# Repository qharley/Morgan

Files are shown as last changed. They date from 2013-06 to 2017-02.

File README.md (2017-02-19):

RepRAP Morgan Classic
======

RepRAP Morgan scad source repository
GPLv2 2013

This is the source of the original Morgan design.
See the RepRapMorgan organisation for new versions.
https://github.com/RepRapMorgan

Lilian is the latest open sourced version at the time of writing.

Please find more information on this project at its web home http://www.morgan3dp.com

Please feel free to use it to make your own Morgan.

Quentin Harley

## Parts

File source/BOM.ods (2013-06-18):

Component | Quantity
01-pvc_pipe_support_a | 4
02-pvc_pipe_support_b | 4
03-z_mount_bottom_8mm | 1
04-z_mount_top_8mm | 1
05-motormount_short | 1
06-motormount_tall | 1
07-drivewheel_rod | 1
08-drivewheel_tube | 1
09-22mm_6805_bearing_adaptor | 1
10-bed_arm_left_8mm | 1
11-bed_arm_right_8mm | 1
12-bed_z_mount_bracket | 1
13-bed_rear_mountclips | 2
15mm pipe holders – To be done | 2
15-hall_endstop_holder | 3
16-leadscrew_shaft_motor_mount | 1
17-Morgan_arm_PSI_a | 1
18-Morgan_arm_PSI_b | 1
19-Morgan_arm_Theta_a | 1
20-Morgan_arm_Theta_b | 1
21-Morgan_toolhead | 1
22-Leadscrew-nut_Alpen8mmSDS | 1
23-extruder_bowden_adaptor | 1
Cap_2 | 2
Eckstruder_Big_Gear_Herringbone | 1
Eckstruder_Block_for_Prusa | 1
Eckstruder_Idler_Block_for_Prusa | 1
Eckstruder_Small_Gear_Herrinbone | 1
thumb_knob_M4_extruder | 1
TighteningCone_2 | 2
M8 nut | 12
M8 washer | 6
M8 spring washer | 10
M8 washer 28mm | 6
M4 nut | 9
M4 bolt 40mm | 8
M4 bolt 80mm | 1
M8 Nylock Nut | 6
M8 Bolt 40mm | 3
M8 Bolt 100mm | 1
M8 Bolt 60mm | 1
PVC pipe 32mm OD 459mm | 2
PVC pipe 32mm OD 452mm | 2
2mm self tapping coach screws, 40mm | 2
15mm brass pipe 440mm | 1
15mm brass pipe 200mm | 2
22mm brass pipe 460mm | 1
8mm threaded rod 650mm | 1
8mm smooth rod | 2
608z | 5
F608z | 4
hard spring (idler compression) 7mm | 1
8mm soft spring (lead screw anti backlash | 1
cabinet coach screws, 5mm | 10
LM8uu bearing or alternative | 4
lead screw 330mm | 1
M3 nut | 3
M3 grub screw 6mm (or suitable replacement bolt | 3
hall effect endstop sensors | 3
Electronics | 1
Pololu low current 1/16th | 2
Pololu high current 1/32th | 2
Step motor 200step (1.8deg) | 2
Step motor 400step (0.9deg (if possible – otherwise increase other motors) | 2
Power supply AXT 400W minimum | 1
PTFE tube 6mm 600mm | 1
Additional PTFE tube 4mm 600mm (Only if 1.75mm J-head) | 1
Morgan lasercut platforms | 1
Universal build plate | 1
Mk2a heatbed | 1
aluminium build surface | 1
Ethernet cable, multistrand flexible, m | 5
High current cable, heatbed m | 1

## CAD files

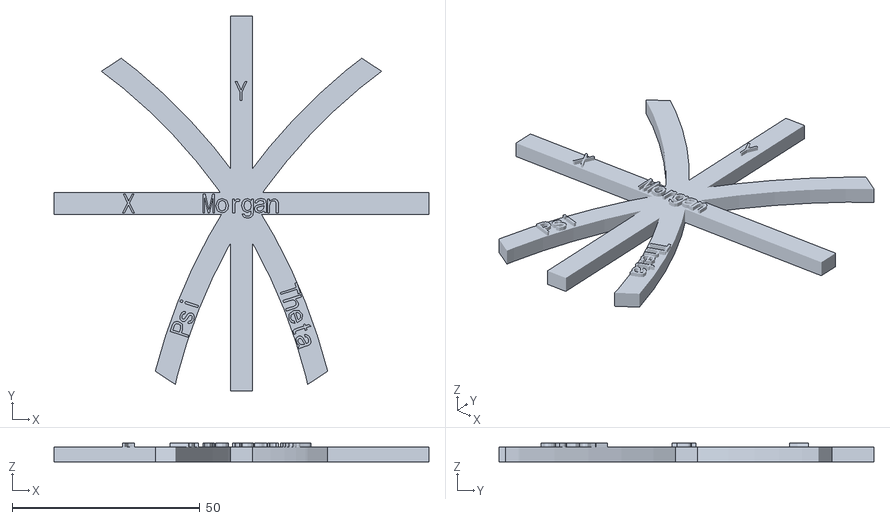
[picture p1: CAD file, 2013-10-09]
calibration/SCARA-CAL.stl
100.0 x 100.0 x 5.00

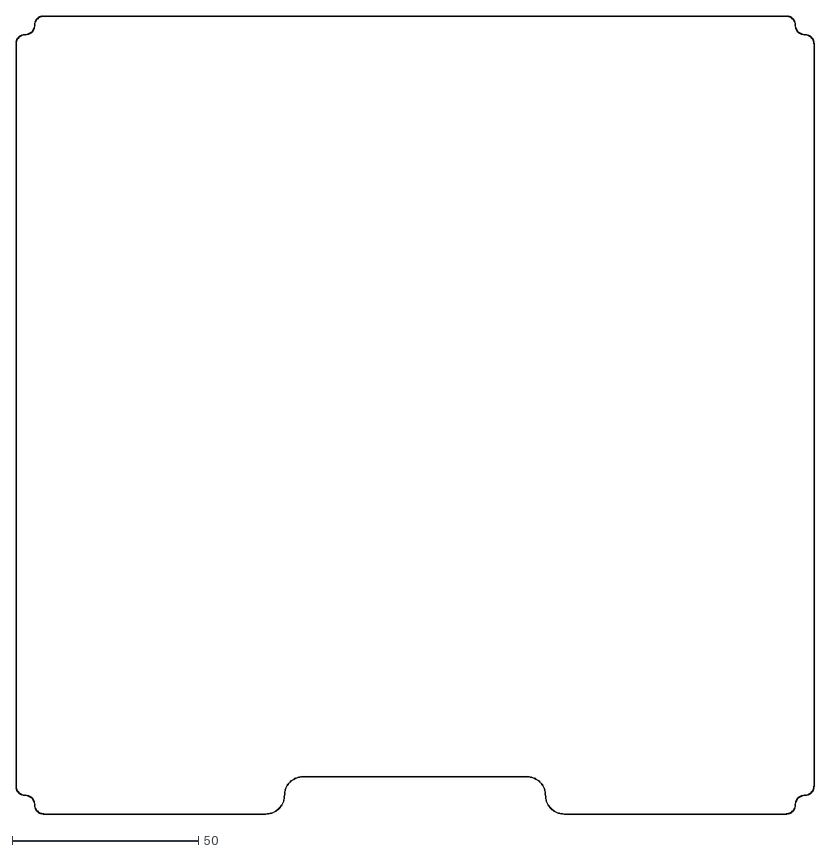
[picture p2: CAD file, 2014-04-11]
dxf/BuildPlate4_by_gineer.dxf
214.0 x 214.0

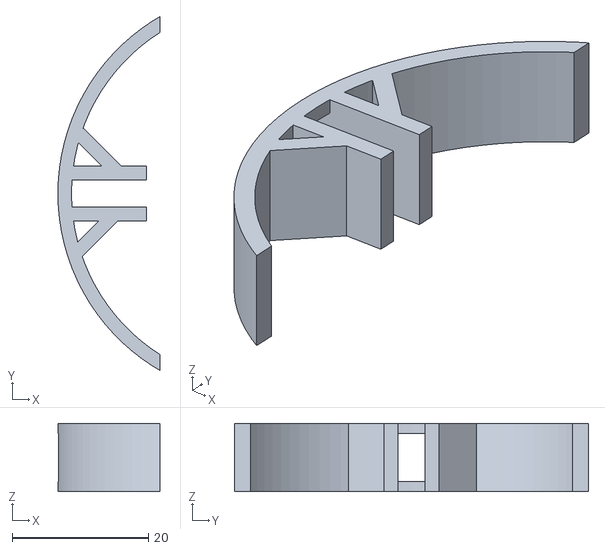
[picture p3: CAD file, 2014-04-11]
source/belt clip.stl
15.0 x 51.9 x 10.0

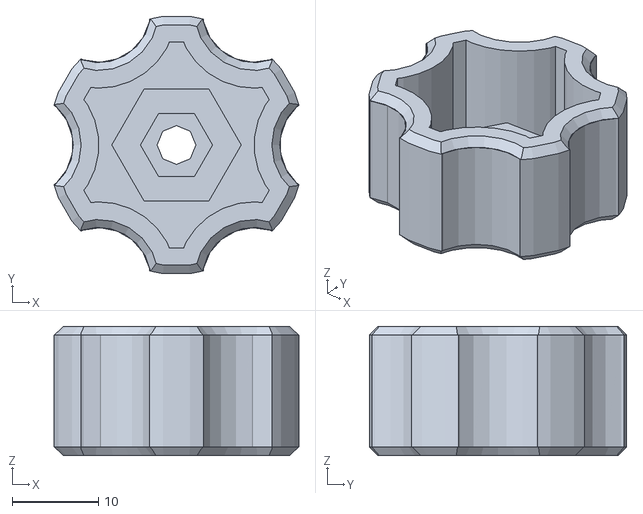
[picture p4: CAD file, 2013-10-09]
stl/Eckstruder-3mm/thumb_knob_M4_extruder.stl
28.4 x 29.8 x 15.0

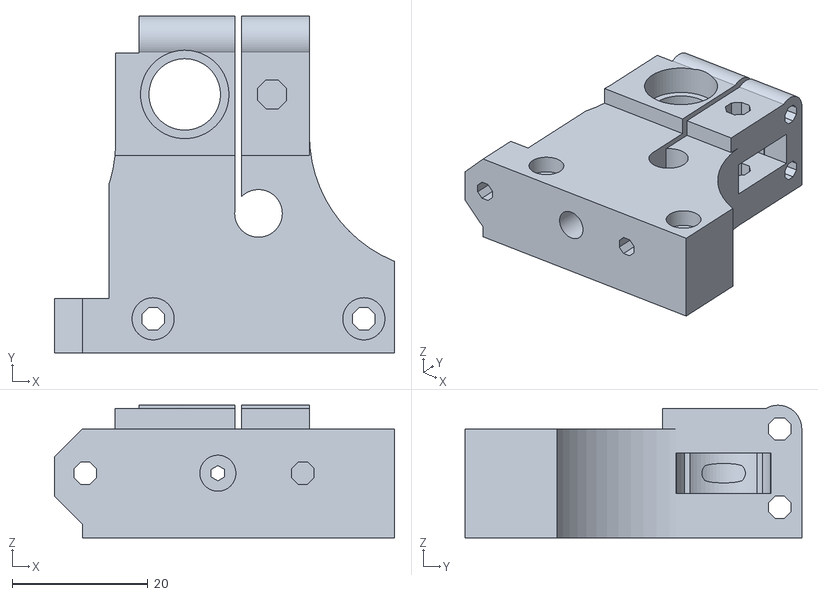
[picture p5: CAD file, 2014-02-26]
stl/Morgan-extruder-1.75mm/extruder-drive-1off.stl
50.0 x 49.5 x 19.5

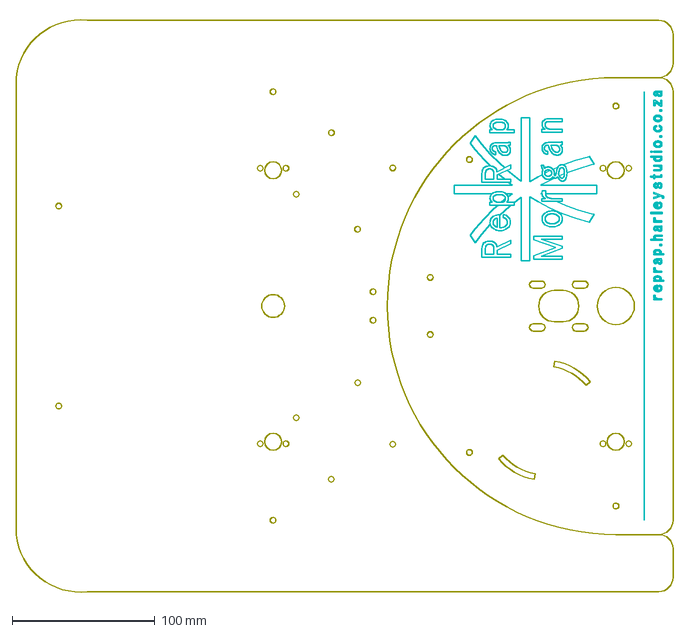
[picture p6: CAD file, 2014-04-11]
dxf/platform_cut_engrave_mk2.dxf
460.0 x 404.1 mm

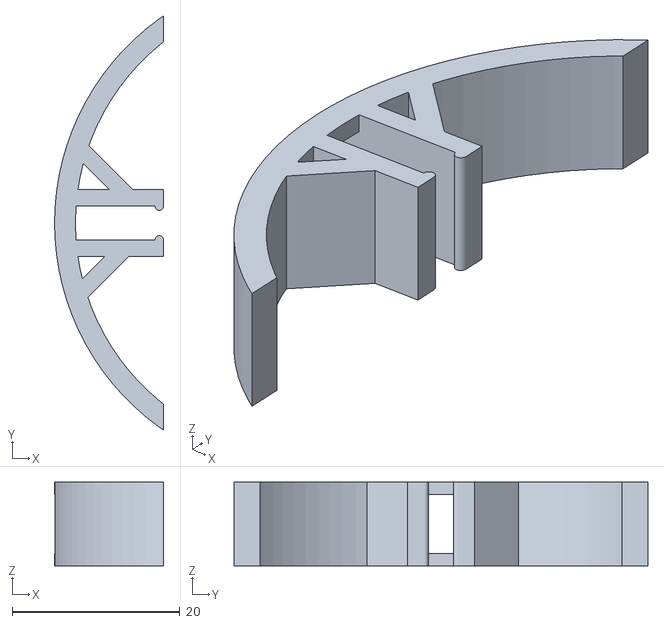
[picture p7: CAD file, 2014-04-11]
stl/28-Morgan_belt_clip.stl
13.0 x 49.4 x 10.0

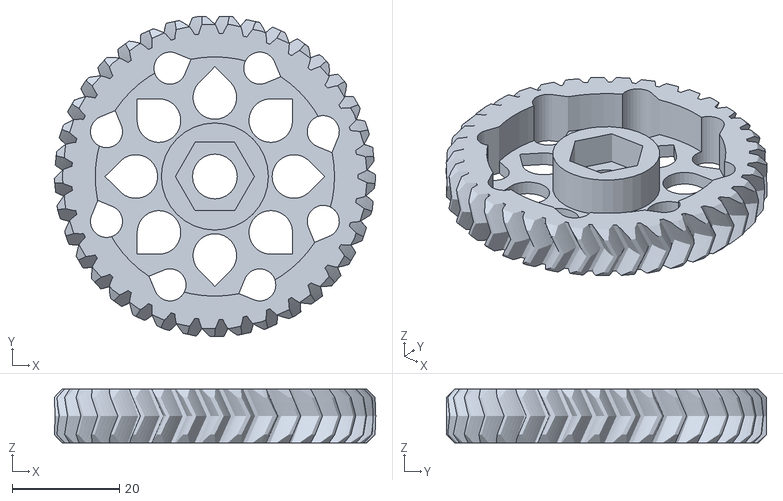
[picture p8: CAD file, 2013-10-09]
stl/Eckstruder-3mm/Eckstruder_Big_Gear_Herringbone.stl
60.1 x 59.8 x 10.0

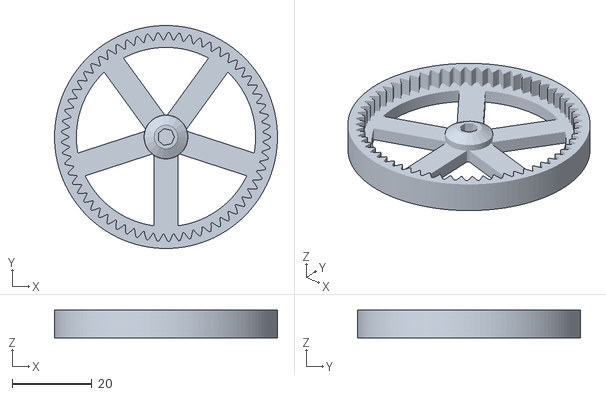
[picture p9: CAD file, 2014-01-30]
stl/Morgan-extruder-1.75mm/large-gear-1off.stl
56.0 x 56.0 x 7.00

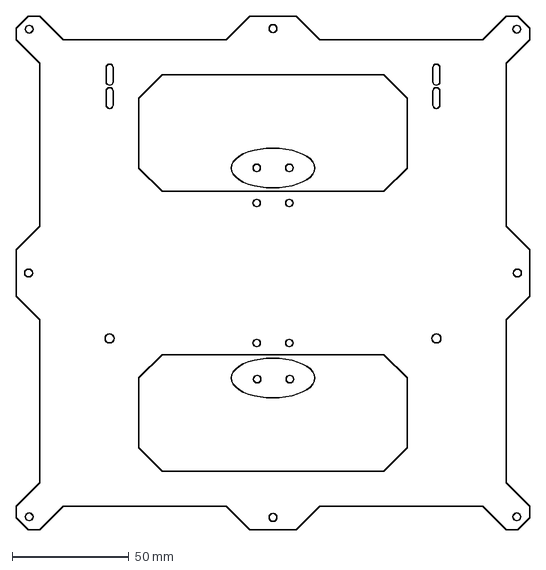
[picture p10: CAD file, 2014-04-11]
dxf/Morgan_bed_base.dxf
220.0 x 220.0 mm

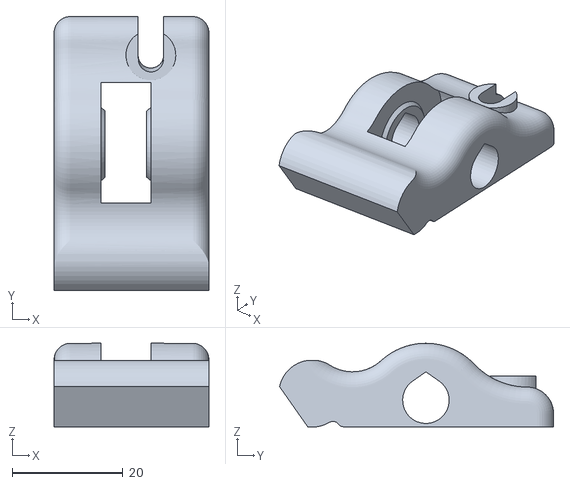
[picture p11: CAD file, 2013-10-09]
stl/Eckstruder-3mm/Eckstruder_Idler_Block_for_Prusa.stl
28.0 x 49.5 x 15.1

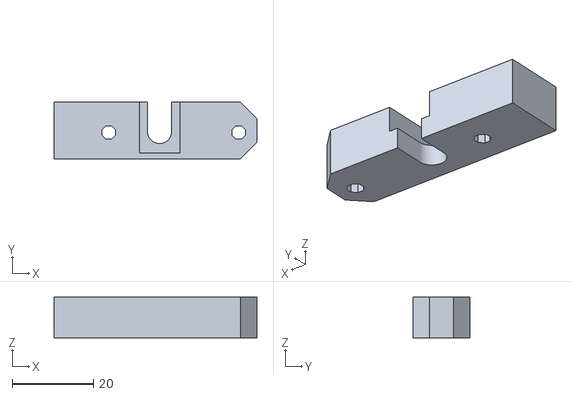
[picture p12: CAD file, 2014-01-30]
stl/Morgan-extruder-1.75mm/6mm-ptfe-clamp-1off.stl
50.0 x 14.0 x 10.0

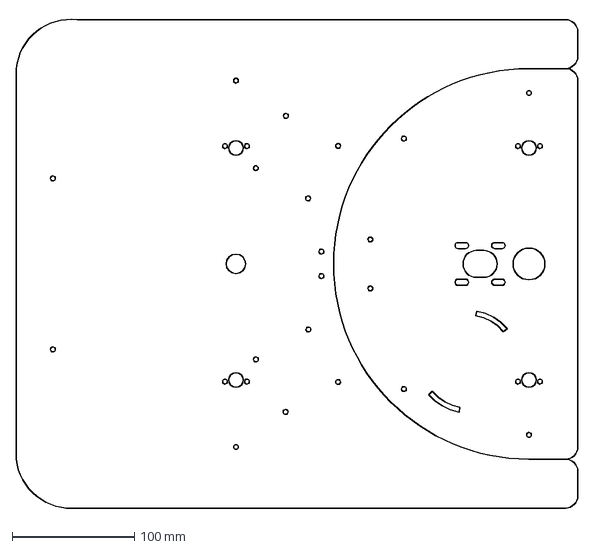
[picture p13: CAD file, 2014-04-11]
dxf/platform_cut_mk2.dxf
460.0 x 404.1 mm

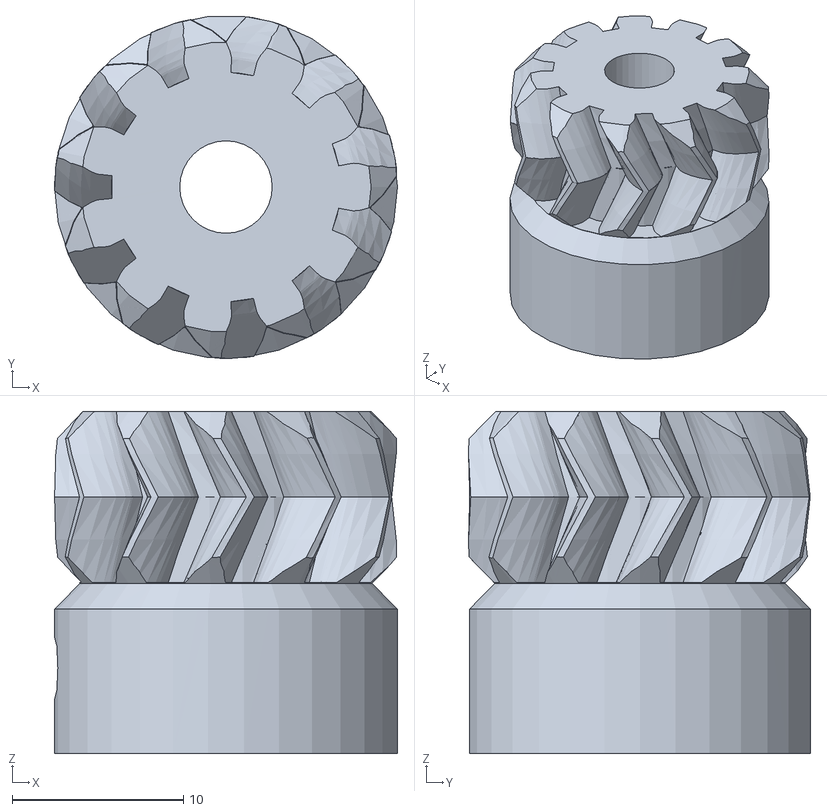
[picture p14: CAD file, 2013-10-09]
stl/Eckstruder-3mm/Eckstruder_Small_Gear_Herringbone.stl
20.0 x 20.0 x 20.0

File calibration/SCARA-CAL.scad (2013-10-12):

// Morgan SCARA Calibration phantom

use <Writescad/Write.scad>;   // get it here... http://www.thingiverse.com/thing:16193
use <MCAD/polyholes.scad>;
Linkage = 150;	//	Arm segment nominal length (as programmed in Firmware)

xoffset = -35;	// Scara tower offset (as programmed in firmware)
yoffset = -65;

K1 = 0;
K2 = 0;

theta = 0;
psi = 0;

xpos = 125.27;
ypos = 82.5;

cal_angle = 33.367;

arm_width = 6;
arm_height = 4;



//projection(cut = false)
	SCARAcal();

$fn=100;

module SCARAcal(){


	intersection(){
		translate([-xpos,ypos+yoffset,-1])
			difference(){
				cylinder(r=Linkage + 3, h=arm_height+2);
				cylinder(r=Linkage - 3, h=arm_height+2);
	
			}
		translate([-xpos,ypos+yoffset,0])
		rotate([0,0,cal_angle])
			translate([100,-50,0])
				cube([100,100,arm_height]);
	}

	intersection(){
		translate([xpos,ypos+yoffset,-1])
			difference(){
				cylinder(r=Linkage + arm_width/2, h=arm_height+2);
				cylinder(r=Linkage - arm_width/2, h=arm_height+2);
	
			}
		translate([xpos,ypos+yoffset,0])
		rotate([0,0,180-cal_angle])
			translate([100,-50,0])
				cube([100,100,arm_height]);
	}

	translate([0,100,arm_height/2]){
		cube([100,arm_width,arm_height],center=true);
		cube([arm_width,100,arm_height],center=true);
	}

	translate([16,70,arm_height])
		#write("Theta",t=2,h=6,rotate=72,center=true);

	translate([-16,70,arm_height])
		#write("Psi",t=2,h=6,rotate=-72,center=true);

	translate([0,130,arm_height])
		#write("Y",t=2,h=7,rotate=0,center=true);

	translate([-30,100,arm_height])
		#write("X",t=2,h=7,rotate=90,center=true);

	translate([0,101,arm_height])
		#write("Morgan",t=2,h=6,rotate=0,center=true);
	
}

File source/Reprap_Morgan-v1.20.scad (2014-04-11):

//---------------------------------------------------------------------------------------------------
// RepRap "Morgan", main ver 1.20 - Single extruder version
// Copyright 2012, 2013. Author: Quentin Harley (qharley)
// This original design is licensed under GPLv2.
//
// These are the main SCARA arm components

include <MCAD/teardrop.scad>
include <MCAD/polyholes.scad>
include <MCAD/nuts_and_bolts.scad>

LMxUU = 8;				// Choose linear bearing: 8 or 12mm
rodspacing = 175;		// Distance between rods:	175 standard, 190 wide
PVC_pipe_OD = 32;		// Default 32mm
PVC_pipe_ID = 27.5;	// measure pipe ID to adjust
Drive_pipe_OD = 22.5;	// Drive pipe outter diameter: 22mm default
THREADLESS = false;	// True for use of threadless ball screw in z-bracket
SUPPORTED_ROD = true;	// Rods held by Z-mounts - False for platform mounted (lasercut)
Leadnut_thread = false;// Apply the thread of the leadscrew nut to the Z coupler

ENVELOPE_CHECK = false;

MakeMorgan(05);		// Select Part number to make	

//MorganEndstopZ();
//***********************************************************
//**                                                			**
//**    Select the number of the module to make				**
//**																		**
//**	01:	 PVC pipe support A (Ported, 458.5mm pipe)			**
//**	02:	 PVC pipe support B (non Ported, 451.5mm pipe)		**
//**	03: Z-mount Bottom												**
//**	04: Z-mount Top													**
//**	05: Motormount Short											**
//**	06: Motormount Tall											**
//**	07: Rod mounted Drivewheel									**
//**	08: Tube mounted Drivewheel									**
//**	09: 22mm Tube 6805 bearing adaptor							**
//**	10: Bed arm Left												**
//**	11: Bed arm Right												**
//** 	12:	 Bed Z-bracket and lead screw holder					**
//**	13: Bed rear mounting clips									**
//**	14: Bed front mounting clips									**
//**	15: hall-endstop holders										**
//**	16: Z-Lead screw motor shaft coupler						**
//**	17: Arm PSI A (inner supporting arm)						**
//**	18: Arm PSI B (outer supporting arm)						**
//**	19: Arm Theta A (inner steering arm)						**
//**	20: Arm Theta B (outter steering arm)						**
//**	21: Morgan Tool head (make from ABS/Nylon/etc)		**
//**	22: Lead screw nut (Alpen 8mm SDS)	
//**	23: extruder Bowden adaptor
//**  24: Belt anchor clip
//
//**  25: Morgan Line wheel (Rod mount)
//**  26: Morgan Line Wheel (Tube mount)				
//**
//**  TO DO!  Build Plates...
//**		Select number of build plate
//**	50: Arms Plate 		(PLA)
//**	51: Bed Plate 1		(PLA)
//**	52: Bed Plate 2		(PLA)
//**	55: Wheel PlateA	(PLA)
//**	56: Wheel PlateB	(PLA)
//**	60: Diverse Plate	(ABS)



module MakeMorgan(partnumber)
{
	if (partnumber == 1 ){
		MorganPVCsupport_ANG(PVC_pipe_ID,130,130,420, pipe = false, port=true);	// 458.47
	}
	if (partnumber == 2 ){
		MorganPVCsupport_ANG(PVC_pipe_ID,70,150,420, pipe = false);					// 451.44
	}
	
  rotate([0,0,45]){ 					// parts rotated through 45deg to ease fitting to RepRap heatbed


//MorganPillarMount();
//MorganShaftMount();
	if (partnumber == 3 ){
		if (SUPPORTED_ROD){
			MorganZmountBot(rodspacing, LMxUU);
		}
		else {
			MorganShaftMount();
		}		
	}
	if (partnumber == 4 ){
		if (SUPPORTED_ROD){
			MorganZmountTop(rodspacing, LMxUU);
		}
		else {
			MorganPillarMount();
		}	
		
	}

  }

	if (partnumber == 5 ){
		MorganMotorMount4(Height = 50);
	}
	if (partnumber == 6 ){
		mirror()
			MorganMotorMount4(Height = 70);
	}
	if (partnumber == 7 ){
		MorganBeltWheel();			// Rod mounted belt drive wheel
	}
	if (partnumber == 25 ){
		MorganLineWheel();			// Rod mounted line drive wheel
	}
	if (partnumber == 8 ){
		MorganBeltWheel2();			// Tube mounted belt drive wheel
	}
	if (partnumber == 26 ){
		MorganLineWheel2();			// Tube mounted line drive wheel
	}
	if (partnumber == 9 ){
		MorganPillar();				// 6805 bearing tube mount
	}
	
  rotate([0,0,45]){

	if (partnumber == 10 ){
		if(LMxUU == 12)
			MorganBedarmLeft(21.5);
		else
			MorganBedarmLeft(15.5);
	}
	if (partnumber == 11 ){
		if(LMxUU == 12)
			MorganBedarmRight(21.5);
		else
			MorganBedarmRight(15.5);
	}
	if (partnumber == 12 ){
		//Bed_stabil_bracket(21.5);
		if(LMxUU == 12)
			Bed_stabil_bracket(21.5);
		else
			Bed_stabil_bracket(15.5);
	}

  }

	if (partnumber == 13 ){
		BedMountRear();
	}
	if (partnumber == 14 ){
		BedMountFront();
	}
	
	if (partnumber == 15 ){
		MorganEndstop();
	}

	if (partnumber == 16 ){
		rotate([0,0,45])
			MorganZCoupler();
	}
	if (partnumber == 17 ){
		Primary_Arm();
	}
	if (partnumber == 18 ){
		Secondary_Arm();
	}
	if (partnumber == 19 ){
		Sup_Arm1();
	}	
	if (partnumber == 20 ){
		Sup_Arm2();
	}
	if (partnumber == 21 ){
		//Secondary_Arm_hotend_holder_mk2(Hotend_D = 16.5, Hotend_H = 12);
		Secondary_Arm_hotend_holder_mk2(Hotend_D = 16.5, Hotend_H = 12+25,mountpiece = true);
	}
	if (partnumber == 22 ){
		leadscrew_nut();
	}
	if (partnumber == 23 ){
		Extruder_Bowden_adaptor(support = false);
	}
	if (partnumber == 24 ){
		belt_clip();;
	}

	
//**************** Plates  ***************************

	if (partnumber == 50 ){
		translate([0,0,0])
			Primary_Arm();
		translate([0,35,0])
			Secondary_Arm();
		translate([0,-35,0])
			Sup_Arm1();
		translate([0,73,0])
			Sup_Arm2();
		
	}

	if (partnumber == 51 ){
		rotate([0,0,45]){
			translate([-13,0,0])
				if(LMxUU == 12)
					MorganBedarmLeft(21.5);
				else
					MorganBedarmLeft(15.5);

			translate([13,0,0])
				if(LMxUU == 12)
					MorganBedarmRight(21.5);
				else
					MorganBedarmRight(15.5);
		}

		translate([0,60,0])
			BedMountRear();
		translate([-40,150,0])
			rotate([0,0,180])
				BedMountRear();

		translate([-120,50,15/2])
			BedMountFront();
		translate([-120,20,15/2])
			BedMountFront();

	}


	if (partnumber == 60 ){
		translate([0,0,0])
			rotate([0,0,0])
				Secondary_Arm_hotend_holder(Hotend_D = 16.5, Hotend_H = 12);

		translate([70,-10,0])
			rotate([0,0,180])
				MorganPVCsupport_ANG(26.5,130,130,420, pipe = false, port=true);	// 458.47
	
		translate([-40,0,0])
			rotate([0,0,180])
				MorganPVCsupport_ANG(26.5,130,130,420, pipe = false, port=true);	// 458.47

		translate([-50,40,0])
			rotate([0,0,0])
				MorganPVCsupport_ANG(26.5,70,150,420, pipe = false);					// 451.44
		
		translate([-50,-70,0])
			rotate([0,0,0])
				MorganPVCsupport_ANG(26.5,70,150,420, pipe = false);					// 451.44

		translate([-70,-40,0])
			rotate([0,0,0])
				Extruder_Bowden_adaptor(support = false);

		translate([40,-35,0])
			rotate([0,0,0])
				import("../stl/cap_2.stl");

		translate([-40,-35,0])
			rotate([0,0,0])
				import("../stl/cap_2.stl");

		translate([-30,50,0])
			rotate([0,0,0])
				import("../stl/Eckstruder_Big_Gear_Herringbone.stl");

		translate([-16,-35,20])
			rotate([0,0,0])
				import("../stl/Eckstruder_Small_Gear_Herringbone.stl");

		translate([-50,-25,0])
			rotate([0,0,-90])
				import("../stl/Eckstruder_Idler_Block_for_Prusa.stl");

		translate([50,-65,0])
			rotate([0,0,0])
				import("../stl/thumb_knob_M4_extruder.stl");

		translate([10,110,0])
			rotate([0,0,-90])
				import("../stl/Eckstruder_Block_for_Prusa.stl");

	}

}





// **********************************************************
// **  Here be dragons...

//** print envelope check - only in F5 review
if(ENVELOPE_CHECK){
	translate([0,0,50])
		%cube([200,200,100], center=true);
}

module Matrix_test()
{
	for(x=[0:9])
	{
		for (y=[0:9])
		{
			translate([20*x,20*y,1.5])
				difference(){
					cube([20,20,3], center=true);
					cube([19,19,3],center=true);
				}
		}
	}	
}



PipeFactor = 40/39.2;			// Multiplication factor for inner diameter 

//MorganFrame();

pipeselect = false; // Show pipes in frame... default false


// ************** Building Blocks *************
// MorganPillarMount();
//	MorganShaftMount();
// MorganBedarm_mount();
//Bed_stabil_clasp();

// *****************8***********
//MorganMotorMount(50);
//MorganMotorMount(75);
//MorganFlatMotorMount();

module Dual_toohead()
{
	MakeMorgan(21);		// Select Part number to make	

	translate([150,0,0])
		rotate([0,0,12])
			translate([-150,0,0])
				rotate([0,0,90-(12/2)])
					Secondary_Arm_hotend_holder_2(Hotend_D = 16.5, Hotend_H = 12);
	translate([0,0,27])
		rotate([0,0,50])
			#MakeMorgan(20);
	translate([0,0,2])
		#MakeMorgan(18);
}

module leadscrew_profile()
{
	projection(cut=false){
		//polyhole(5,5);
		cylinder(r=3, h=5, $fn=24);
		cube([7.5, 3,1], center=true);
		rotate([0,0,-45])
			cube([6.5,3,1],center = true);
	}
}

module leadscrew_nut(){
	difference(){
		union(){
			cylinder(r=14.8/2,h=14, $fn=6);

		}
		linear_extrude(height = 120/4, center = true, twist = -360)
			scale(1.1)
				leadscrew_profile();
	}

}

module belt_clip($fn = 100)		// Adapted from code by WJ Harley
{
	difference()	{
		translate([0,0,0])	
			cylinder(10,30,30,0);
		union()
		{	
			translate([-17,-30,-1])
				cube([50,65,12]);
			translate([0,0,-0.2])	
				cylinder(12,r=27.5);
			translate([-35,-2,1.5])
				cube([30,4,7]);
		}
	}
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

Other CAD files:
stl/Morgan-extruder-1.75mm/spacer-1off.stl
dxf/OpenHW_Universal-XPlate.dxf
stl/05-motormount_short_mk5.stl
stl/Eckstruder-3mm/Eckstruder_Block_for_Prusa.stl
source/Reprap_Morgan-v1.00.scad
source/Reprap_Morgan-v1.10.scad
dxf/Morgan_platform_cutting.dxf
stl/01-pvc_pipe_support_a.stl
stl/02-pvc_pipe_support_b.stl
stl/03-z_mount_bottom_12mm.stl
stl/03-z_mount_bottom_8mm.stl
stl/03-z_mount_bottom_noarm.stl
stl/04-z_mount_top_12mm.stl
stl/04-z_mount_top_8mm.stl
stl/04-z_mount_top_nosup.stl
stl/05-motormount_short.stl
stl/06-motormount_tall.stl
stl/06-motormount_tall_mk5.stl
stl/07-drivewheel_rod.stl
stl/08-drivewheel_tube.stl
stl/09-22mm_6805_bearing_adaptor.stl
stl/10-bed_arm_left_12mm.stl
stl/10-bed_arm_left_8mm.stl
stl/11-bed_arm_right_12mm.stl
stl/11-bed_arm_right_8mm.stl
stl/12-bed_z_mount_bracket_12mm.stl
stl/12-bed_z_mount_bracket_8mm.stl
stl/13-bed_rear_mountclips.stl
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

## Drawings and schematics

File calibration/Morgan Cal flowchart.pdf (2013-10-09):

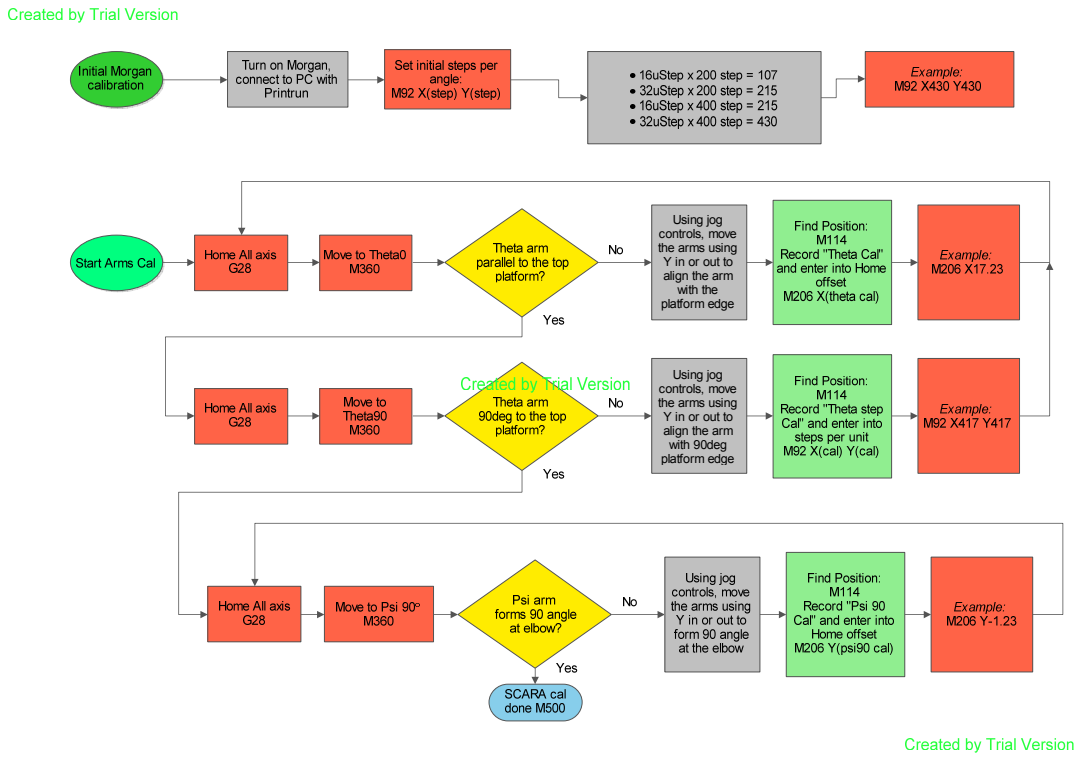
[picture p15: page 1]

Using jog
controls, move
the arms using
Y in or out to
align the arm
with the
platform edge

with 90deg

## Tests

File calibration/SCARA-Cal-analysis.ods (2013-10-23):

Dimension | Measurement |  | Target | Current Step/deg | Scaling Factor | New Step M92 | New factor M365 | after scaling
Theta | 100 | 90.8896776828 | 100.000 | 212.94 |  | 234.28 | 1.1 | 99.979
Psi | 100 | 90.8896776828 | 100.000 | 216.98 |  | 238.73 | 1.1 | 99.979
X | 110 |  | 100.000 |  | 1.023 |  | 0.93 | 100.000
Y | 110 |  | 100.000 |  | 0.998 |  | 0.907 | 99.970
Z

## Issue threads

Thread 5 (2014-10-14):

Straight line drawing

MYasirSheikh, 2014-10-14:
As you know, it's a chunk of code from prepare_move function

Is this part of the code for straight line drawing (since the arm has a tendency of radial movement because of SCARA). If YES, can someone explain me the logic.. I badly need it for some development. help me pleaseeee..

float seconds = 6000 * cartesian_mm / feedrate / feedmultiply;
  int steps = max(1, int(DELTA_SEGMENTS_PER_SECOND * seconds));
  for (int s = 1; s <= steps; s++) {
    float fraction = float(s) / float(steps);
    for(int8_t i=0; i < NUM_AXIS; i++) {
      destination[i] = current_position[i] + difference[i] * fraction;
    }
    calculate_delta(destination);
    plan_buffer_line(delta[X_AXIS], delta[Y_AXIS], delta[Z_AXIS],
                     destination[E_AXIS], feedrate*feedmultiply/60/100.0,
                     active_extruder);
  }

  for(int8_t i=0; i < NUM_AXIS; i++) {
    current_position[i] = destination[i];
  }
}

qharley, 2015-01-02:
It has been quite a while since I did any work on marlin... Mostly my fault since I did not know how to keep the software updated and how to do pull requests.

I have since started working on Smoothieware, and it is a much better platform for axial robots like Morgan, especially because of the superior processing ability of the ARM chip.

Closed 2015-01-03.

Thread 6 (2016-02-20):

Piece 18 Morgan Arm PSI B PLUS Toolhead faulty render.

techboycr, 2016-02-20:
Hi, this is an amazing project, First of all thank you Mr. Harley.

The Piece 18 Morgan Arm PSI B PLUS Toolhead is not quite right at one the piece and extra border that is not present in the arm alone.

I have the the repository and there is no file for it, try to put together my self from the openscad file, but failed miserably...

Is there any formula to make it  or maybe the open scad file itself available somewhere??

techboycr, 2016-02-20:
I am sorry, diidnt check better the part ir there in the build.

Thanks any way!!

Closed 2016-02-20.

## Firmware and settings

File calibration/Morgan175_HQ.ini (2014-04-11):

[profile]
layer_height = 0.1
wall_thickness = 0.8
retraction_enable = True
solid_layer_thickness = 0.6
fill_density = 10
nozzle_size = 0.4
print_speed = 40
print_temperature = 210
print_temperature2 = 0
print_temperature3 = 0
print_temperature4 = 0
print_bed_temperature = 60
support = None
platform_adhesion = None
support_dual_extrusion = Both
wipe_tower = False
wipe_tower_volume = 15
ooze_shield = False
filament_diameter = 1.76
filament_diameter2 = 0
filament_diameter3 = 0
filament_diameter4 = 0
filament_flow = 100.0
retraction_speed = 60
retraction_amount = 4.5
retraction_dual_amount = 16.5
retraction_min_travel = 1.5
retraction_combing = True
retraction_minimal_extrusion = 0.02
retraction_hop = 0.0
bottom_thickness = 0.2
object_sink = 0.0
overlap_dual = 0.15
travel_speed = 150.0
bottom_layer_speed = 20
infill_speed = 0.0
inset0_speed = 0.0
insetx_speed = 0.0
cool_min_layer_time = 5
fan_enabled = True
skirt_line_count = 1
skirt_gap = 3.0
skirt_minimal_length = 150.0
fan_full_height = 0.5
fan_speed = 100
fan_speed_max = 100
cool_min_feedrate = 10
cool_head_lift = False
solid_top = True
solid_bottom = True
fill_overlap = 15
support_type = Grid
support_angle = 60
support_fill_rate = 15
support_xy_distance = 0.7
support_z_distance = 0.15
spiralize = False
brim_line_count = 20
raft_margin = 5
raft_line_spacing = 1.0
raft_base_thickness = 0.3
raft_base_linewidth = 0.7
raft_interface_thickness = 0.2
raft_interface_linewidth = 0.2
fix_horrible_union_all_type_a = True
fix_horrible_union_all_type_b = False
fix_horrible_use_open_bits = False
fix_horrible_extensive_stitching = False
plugin_config = (lp1
	.
object_center_x = -1
object_center_y = -1

[alterations]
start.gcode = ;Sliced at: {day} {date} {time}
	;Basic settings: Layer height: {layer_height} Walls: {wall_thickness} Fill: {fill_density}
	;Print time: {print_time}
	;Filament used: {filament_amount}m {filament_weight}g
	;Filament cost: {filament_cost}
	M190 S{print_bed_temperature} ;Uncomment to add your own bed temperature line
	M109 S{print_temperature} ;Uncomment to add your own temperature line
	G21        ;metric values
	G90        ;absolute positioning
	M82        ;set extruder to absolute mode
	M107       ;start with the fan off
	G28 X0 Y0  ;move X/Y to min endstops
	G28 Z0     ;move Z to min endstops
	G1 Z15.0 F{travel_speed} ;move the platform down 15mm
	G92 E0                  ;zero the extruded length
	G1 F200 E10              ;extrude 10mm of feed stock
	G92 E0                  ;zero the extruded length again
	G1 F{travel_speed}
	;Put printing message on LCD screen
	M117 Printing...
end.gcode = ;End GCode
	M104 S0                     ;extruder heater off
	M140 S0                     ;heated bed heater off (if you have it)
	G91                                    ;relative positioning
	G1 E-1 F300                            ;retract the filament a bit before lifting the nozzle, to release some of the pressure
	G1 Z+0.5 E-5 X-20 Y-20 F{travel_speed} ;move Z up a bit and retract filament even more
	G28 X0 Y0                              ;move X/Y to min endstops, so the head is out of the way
	M84                         ;steppers off
	G90                         ;absolute positioning
start2.gcode = ;Sliced at: {day} {date} {time}
	;Basic settings: Layer height: {layer_height} Walls: {wall_thickness} Fill: {fill_density}
	;Print time: {print_time}
	;Filament used: {filament_amount}m {filament_weight}g
	;Filament cost: {filament_cost}
	;M190 S{print_bed_temperature} ;Uncomment to add your own bed temperature line
	;M104 S{print_temperature} ;Uncomment to add your own temperature line
	;M109 T1 S{print_temperature2} ;Uncomment to add your own temperature line
	;M109 T0 S{print_temperature} ;Uncomment to add your own temperature line
	G21        ;metric values
	G90        ;absolute positioning
	M107       ;start with the fan off
	G28 X0 Y0  ;move X/Y to min endstops
	G28 Z0     ;move Z to min endstops
	G1 Z15.0 F{travel_speed} ;move the platform down 15mm
	T1                      ;Switch to the 2nd extruder
	G92 E0                  ;zero the extruded length
	G1 F200 E10             ;extrude 10mm of feed stock
	G92 E0                  ;zero the extruded length again
	G1 F200 E-{retraction_dual_amount}
	T0                      ;Switch to the first extruder
	G92 E0                  ;zero the extruded length
	G1 F200 E10             ;extrude 10mm of feed stock
	G92 E0                  ;zero the extruded length again
	G1 F{travel_speed}
	;Put printing message on LCD screen
	M117 Printing...
end2.gcode = ;End GCode
	M104 T0 S0                     ;extruder heater off
	M104 T1 S0                     ;extruder heater off
	M140 S0                     ;heated bed heater off (if you have it)
	G91                                    ;relative positioning
	G1 E-1 F300                            ;retract the filament a bit before lifting the nozzle, to release some of the pressure
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

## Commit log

2013-05-13 new file: dxf/platform_cutting.dxf new file: source/Base_and_Riser_2.stl new file: source/Reprap_Morgan-v1.00.scad new file: stl/01-pvc_pipe_support_a.stl new file: stl/02-pvc_pipe_support_b.stl new 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
    [01-pvc_pipe_support_a.stl, 02-pvc_pipe_support_b.stl, 03-z_mount_bottom_8mm.stl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]
2013-06-08 Included spool holder STL
    [Reprap_Morgan-v1.00.scad]
2013-06-18 12mm smooth rod and LM12uu option included. Improved Z-bracket for the bed arms.
    [Reprap_Morgan-v1.00.scad, platform_cutting.dxf]
2013-06-18 stl included
    [03-z_mount_bottom_12mm.stl, 04-z_mount_top_12mm.stl, 10-bed_arm_left_12mm.stl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]
2013-06-24 Improved DXF for platform. Added motor and fan mounting points
    [platform_cutting.dxf]
2013-06-24 Improved safety of lasercut parts on request
    [platform_cutting.dxf]
2013-06-25 Included Universal build plate to DXF
2013-06-25 Included Bed front mounting clips to STL
    [14-bed_front_mountclips.stl, Reprap_Morgan-v1.00.scad]
2013-06-25 final check-in
    [Reprap_Morgan-v1.00.scad]
2013-07-11 repaired all stl files preventatively
    [01-pvc_pipe_support_a.stl, 02-pvc_pipe_support_b.stl, 03-z_mount_bottom_12mm.stl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]
2013-07-17 fixed platform dxf: mounting hole spacing and rasterised text to make it font independent.
    [platform_cutting.dxf]
2013-07-21 Adding dimentions
    [#platform_cutting.dxf]
2013-07-24 New 12mm z mount bracket, and re-added 8mm bracket.
    The Z-bed mount STL was outdated, causing sizing issues.
    [12-bed_z_mount_bracket.stl, 12-bed_z_mount_bracket_12mm.stl, 12-bed_z_mount_bracket_8mm.stl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]
2013-08-16 8 and 12mm /hall holders STL
    [15-hall_endstop_holder_12mm.stl]
2013-08-18 Improved messages around calibration
    [01-pvc_pipe_support_a.stl, Reprap_Morgan-v1.00.scad]
2013-08-31 modified: source/Reprap_Morgan-v1.00.scad
    [Reprap_Morgan-v1.00.scad]
2013-09-09 Improved PVC pipe holders, and simplified z-bracket for lead screw.
    [01-pvc_pipe_support_a.stl, 02-pvc_pipe_support_b.stl, 12-bed_z_mount_bracket_8mm.stl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]
2013-10-09 modified: source/Reprap_Morgan-v1.00.scad new file: source/Reprap_Morgan-v1.10.scad new file: source/lib/Threadless_Ballscrew_customizable/Threadless_Ballscrew-608zz-m5-m8.stl new file: source/lib/Th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
    [01-pvc_pipe_support_a.stl, 02-pvc_pipe_support_b.stl, 03-z_mount_bottom_12mm.stl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]
2013-10-09 Add calibration phantom and assistant spreadsheet to calculate steps per angle.
    Changes to be committed:
    new file: calibration/Morgan Cal flowchart.pdf
    new file: calibration/SCARA-CAL.scad
    new file: calibration/SCARA-CAL.stl
    new file: calibration/SCARA-Cal-analysis.ods
    [SCARA-CAL.scad, SCARA-CAL.stl, SCARA-Cal-analysis.ods]
2013-10-12 modified: calibration/SCARA-CAL.scad modified: calibration/SCARA-Cal-analysis.ods
    [SCARA-CAL.scad, SCARA-Cal-analysis.ods]
2013-10-23 modified: calibration/SCARA-Cal-analysis.ods modified: source/Reprap_Morgan-v1.00.scad modified: source/Reprap_Morgan-v1.10.scad
    [Reprap_Morgan-v1.00.scad, Reprap_Morgan-v1.10.scad, SCARA-Cal-analysis.ods]
2013-10-26 Added initial Slic3r 0.9.11-dev compatible Morgan printing profiles to the calibration folder
    new file: calibration/dot.Slic3r/filament/1.75 PLA.ini
    new file: calibration/dot.Slic3r/filament/3mm ABS.ini
    new file: calibration/dot.Slic3r/filament/3mm PLA.ini
    new file: calibration/dot.Slic3r/print/LQ 15% Hex Standard.ini
    new file: calibration/dot.Slic3r/print/MQ 15% Hex Standard.ini
    new file: calibration/dot.Slic3r/printer/Morgan 175.ini
    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
2013-12-14 Slimmed down parts, improved motormounts.
    modified: source/Reprap_Morgan-v1.00.scad
    modified: source/Reprap_Morgan-v1.10.scad
    modified: stl/03-z_mount_bottom_8mm.stl
    modified: stl/05-motormount_short.stl
    modified: stl/06-motormount_tall.stl
    modified: stl/07-drivewheel_rod.stl
    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
    [03-z_mount_bottom_8mm.stl, 05-motormount_short.stl, 06-motormount_tall.stl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]
2014-01-26 Added improvements to key parts renamed: dxf/#platform_cutting.dxf -> dxf/platform_cutting.dxf new file: obj/07-drivewheel_rod_fixed.obj modified: source/Reprap_Morgan-v1.00.scad modified: source/Rep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
    [#platform_cutting.dxf, 50-Morgan_arms_plate.stl, 51-Morgan_bed_plate1.stl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]
2014-01-30 Added 1.75mm extruder STL
    renamed: stl/Eckstruder_Big_Gear_Herringbone.stl -> stl/Eckstruder-3mm/Eckstruder_Big_Gear_Herringbone.stl
    renamed: stl/Eckstruder_Block_for_Prusa.stl -> stl/Eckstruder-3mm/Eckstruder_Block_for_Prusa.stl
    renamed: stl/Eckstruder_Idler_Block_for_Prusa.stl -> stl/Eckstruder-3mm/Eckstruder_Idler_Block_for_Prusa.stl
    renamed: stl/Eckstruder_Small_Gear_Herringbone.stl -> stl/Eckstruder-3mm/Eckstruder_Small_Gear_Herringbone.stl
    renamed: stl/thumb_knob_M4_extruder.stl -> stl/Eckstruder-3mm/thumb_knob_M4_extruder.stl
    new file: stl/Morgan-extruder-1.75mm/6mm-ptfe-clamp-1off.stl
    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
    [6mm-ptfe-clamp-1off.stl, Eckstruder_Big_Gear_Herringbone.stl, Eckstruder_Block_for_Prusa.stl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]
2014-02-26 Added updated Morgan 1.75mm extruder block (more gear clearance)
    modified: stl/Morgan-extruder-1.75mm/extruder-drive-1off.stl
    [extruder-drive-1off.stl]
2014-03-25 Added new motor mounts (mk5)
    [05-motormount_short_mk5.stl, 06-motormount_tall_mk5.stl, 21-Morgan_toolhead_mk2.stl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]
2014-04-11 Update: Improved dxf files for laser cutting, including mounting holes for the new motor mounts
    [16-leadscrew_shaft_motor_mount.stl, 16-leadscrew_shaft_motor_mount_alpen.stl, 22-Leadscrew-nut_Alpen8mmSDS.stl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]
2014-06-09 Removed non-functional toolhead
    [21-Morgan_toolhead_mk2.stl]
